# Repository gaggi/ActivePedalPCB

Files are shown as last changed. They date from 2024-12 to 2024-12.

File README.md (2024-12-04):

# Switch-!t ActivePedalPCB
This is a custom PCB designed for the [DIY Force Feedback Pedal](https://github.com/ChrGri/DIY-Sim-Racing-FFB-Pedal). Similar to the V4 PCB from the previously mentioned repository, it is designed to accommodate all the required development and breakout boards. The PCB is built around the Waveshare [ESP32-S3-DEV-Kit-N8R8](https://www.waveshare.com/wiki/ESP32-S3-DEV-KIT-N8R8) and features only five SMD components that need to be soldered by hand.

It is intended to operate via a single USB-B connector for each pedal, powered by a single Meanwell GST360B36-C6P power supply. The power supply can be daisy-chained from one pedal to another. Additionally, the PCB includes space for an optional N7805 step-down converter, enabling all electronics to be powered directly by the power supply. If you choose to solder the N7805, ensure that the 5V connection from the JST-XH header labeled "USB" to the USB-C plug remains unconnected.

# Soldering you PCB
The PCB is designed to allow sub-boards to be attached using female headers or soldered directly to the board. If you opt for direct soldering, follow these steps:
1. Front Side: Start by soldering the SMD components, then solder the pin headers for the ESP32-S3-DEV-KIT-N8R8.
2. Back Side: Solder the ADS1256 module.
3. Front Side: ESP32-S3-DEV-KIT-N8R8: Attach it to the already soldered headers.
   
Once these steps are complete, you can solder all remaining components to the PCB.

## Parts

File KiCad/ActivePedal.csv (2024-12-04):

Reference | Value | Datasheet | Footprint | Qty | DNP | Mouser Part Number | Mouser Price/Stock
J3 | Conn_01x05 | ~ | Connector_JST:JST_XH_B5B-XH-A_1x05_P2.50mm_Vertical | 1
U1 | ESP32-S3-DEV-KIT-N8R8 |  | PCM_Espressif:ESP32-S3-DEV-KIT-N8R8 | 1
U2 | ADS1256_Breakout | http://www.ti.com/lit/ds/symlink/ads1243.pdf | ADS1256_Breakout:ADS1256_Breakout | 1
U3 | ~ |  | Levelshifter_Breakout:Levelshifter_Breakout | 1
J4,J9,J10,J11 | Conn_01x02 | ~ | -- verschiedene Werte -- | 4 |  | 306-B2BXH2TV4LFSN
J1,J5 | Conn_01x04 | ~ | Connector_JST:JST_XH_B4B-XH-A_1x04_P2.50mm_Vertical | 2 |  | 306-B4BXH2TV4LFSN
J2 | Conn_01x03 | ~ | Connector_JST:JST_XH_B3B-XH-A_1x03_P2.50mm_Vertical | 1 |  | 306-BH3BXH2LFSN
J7,J8 | Conn_02x03_Top_Bottom | ~ | Connector_Molex:Molex_Mini-Fit_Jr_5569-06A2_2x03_P4.20mm_Horizontal | 2 |  | 538-26-01-3116
D1 | SS510B | ~ | Diode_SMD:D_SMA-SMB_Universal_Handsoldering | 1 |  | 621-SDT5A50SAF-13
J6 | USB_B | ~ | Connector_USB:USB_B_OST_USB-B1HSxx_Horizontal | 1 |  | 640-USB1030-GF-P-B-B
SW1 | SW_DIP_x02 | ~ | Button_Switch_THT:SW_DIP_SPSTx02_Slide_9.78x7.26mm_W7.62mm_P2.54mm | 1 |  | 655-1825360-1
R1 | 100k | ~ | Resistor_SMD:R_1206_3216Metric_Pad1.30x1.75mm_HandSolder | 1 |  | 708-RNCF1206BTE100K
PS1 | N7805-1PH | https://www.meanwell.com/webapp/product/search.aspx?prod=N78 | N7805-1PH:N78051PH | 1 |  | 709-N7805-1PH | https://www.mouser.co.uk/ProductDetail/MEAN-WELL/N7805-1PH?qs=7D1LtPJG0i2yQtENgJv8Bw%3D%3D
C1 | 10µF | ~ | Capacitor_SMD:CP_Elec_6.3x5.9 | 1 |  | 710-865080743010
C2,C3 | 330µF | ~ | Capacitor_SMD:CP_Elec_10x10 | 2 |  | 710-865230657014

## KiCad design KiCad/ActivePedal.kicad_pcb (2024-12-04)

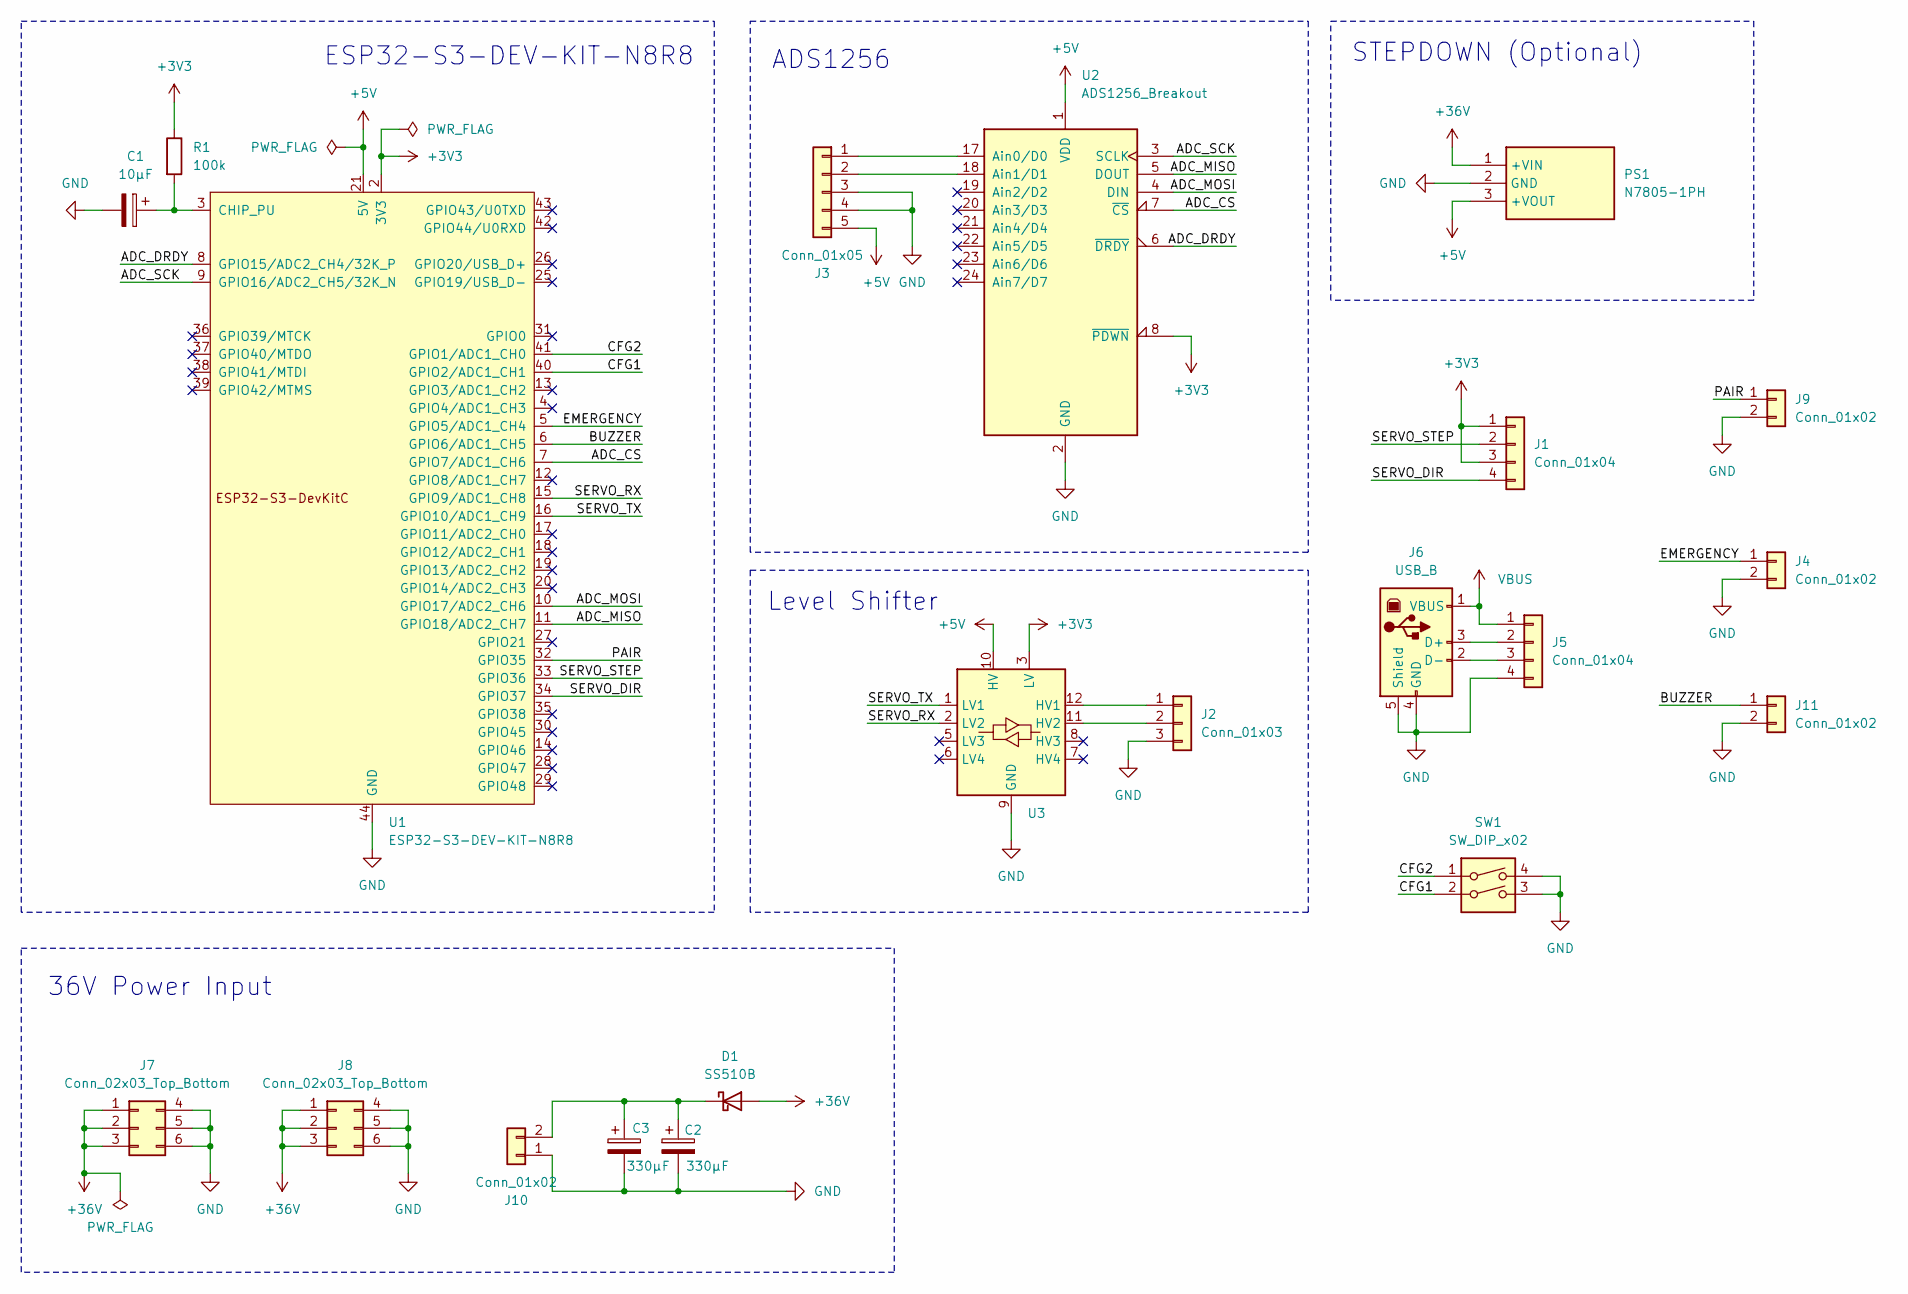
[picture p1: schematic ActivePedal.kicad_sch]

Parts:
C1: 10µF; CP_Elec_6.3x5.9; Mouser Part Number 710-865080743010
C2, C3: 330µF; CP_Elec_10x10; Mouser Part Number 710-865230657014
D1: SS510B; D_SMA-SMB_Universal_Handsoldering; Mouser Part Number 621-SDT5A50SAF-13
J1, J5: Conn_01x04; JST_XH_B4B-XH-A_1x04_P2.50mm_Vertical; Mouser Part Number 306-B4BXH2TV4LFSN
J2: Conn_01x03; JST_XH_B3B-XH-A_1x03_P2.50mm_Vertical; Mouser Part Number 306-BH3BXH2LFSN
J3: Conn_01x05; JST_XH_B5B-XH-A_1x05_P2.50mm_Vertical
J4, J9, J11: Conn_01x02; JST_XH_B2B-XH-A_1x02_P2.50mm_Vertical; Mouser Part Number 306-B2BXH2TV4LFSN
J6: USB_B; USB_B_OST_USB-B1HSxx_Horizontal; Mouser Part Number 640-USB1030-GF-P-B-B
J7, J8: Conn_02x03_Top_Bottom; Molex_Mini-Fit_Jr_5569-06A2_2x03_P4.20mm_Horizontal; Mouser Part Number 538-26-01-3116
J10: Conn_01x02; AMASS_XT30U-F_1x02_P5.0mm_Vertical; Mouser Part Number 306-B2BXH2TV4LFSN
PS1: N7805-1PH; N78051PH; Mouser Part Number 709-N7805-1PH
R1: 100k; R_1206_3216Metric_Pad1.30x1.75mm_HandSolder; Mouser Part Number 708-RNCF1206BTE100K
SW1: SW_DIP_x02; SW_DIP_SPSTx02_Slide_9.78x7.26mm_W7.62mm_P2.54mm; Mouser Part Number 655-1825360-1
U1: ESP32-S3-DEV-KIT-N8R8
U2: ADS1256_Breakout
U3: Levelshifter_Breakout

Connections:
+3V3: J1.1, J1.3, R1.1, U1.1 (3V3), U1.2 (3V3), U2.8 (~PDWN), U3.3 (LV)
+5V: J3.5, PS1.3 (+VOUT), U1.21 (5V), U2.1 (VDD), U3.10 (HV)
+36V: D1.2 (A), J7.1, J7.2, J7.3, J8.1, J8.2, J8.3, PS1.1 (+VIN)
/ADC_CS: U1.7 (GPIO7/ADC1_CH6), U2.7 (~CS)
/ADC_DRDY: U1.8 (GPIO15/ADC2_CH4/32K_P), U2.6 (~DRDY)
/ADC_MISO: U1.11 (GPIO18/ADC2_CH7), U2.5 (DOUT)
/ADC_MOSI: U1.10 (GPIO17/ADC2_CH6), U2.4 (DIN)
/ADC_SCK: U1.9 (GPIO16/ADC2_CH5/32K_N), U2.3 (SCLK)
/BUZZER: J11.1, U1.6 (GPIO6/ADC1_CH5)
/CFG1: SW1.2, U1.40 (GPIO2/ADC1_CH1)
/CFG2: SW1.1, U1.41 (GPIO1/ADC1_CH0)
/EMERGENCY: J4.1, U1.5 (GPIO5/ADC1_CH4)
/PAIR: J9.1, U1.32 (GPIO35)
/SERVO_DIR: J1.4, U1.34 (GPIO37)
/SERVO_RX: U1.15 (GPIO9/ADC1_CH8), U3.2 (LV2)
/SERVO_STEP: J1.2, U1.33 (GPIO36)
/SERVO_TX: U1.16 (GPIO10/ADC1_CH9), U3.1 (LV1)
GND: C1.2, C2.2, C3.2, J2.3, J3.3, J3.4, J4.2, J5.4, J6.4 (GND), J6.5 (Shield), J7.4, J7.5, J7.6, J8.4, J8.5, J8.6, J9.2, J10.1, J11.2, PS1.2 (GND), SW1.3, SW1.4, U1.22 (GND), U1.23 (GND), U1.24 (GND), U1.44 (GND), U2.2 (GND), U2.9 (GND), U2.10 (GND), U2.11 (GND), U2.12 (GND), U2.13 (GND), U2.14 (GND), U2.15 (GND), U2.16 (GND), U3.4 (GND), U3.9 (GND)
unnamed: C2.1, C3.1, D1.1 (K), J10.2
unnamed: J2.1, U3.12 (HV1)
unnamed: J2.2, U3.11 (HV2)
unnamed: J3.1, U2.17 (Ain0/D0)
unnamed: J3.2, U2.18 (Ain1/D1)
unnamed: J5.2, J6.3 (D+)
unnamed: J5.3, J6.2 (D-)
unnamed: C1.1, R1.2, U1.3 (CHIP_PU)
VBUS: J5.1, J6.1 (VBUS)

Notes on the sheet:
ESP32-S3-DEV-KIT-N8R8
ADS1256
36V Power Input
STEPDOWN (Optional)
Level Shifter

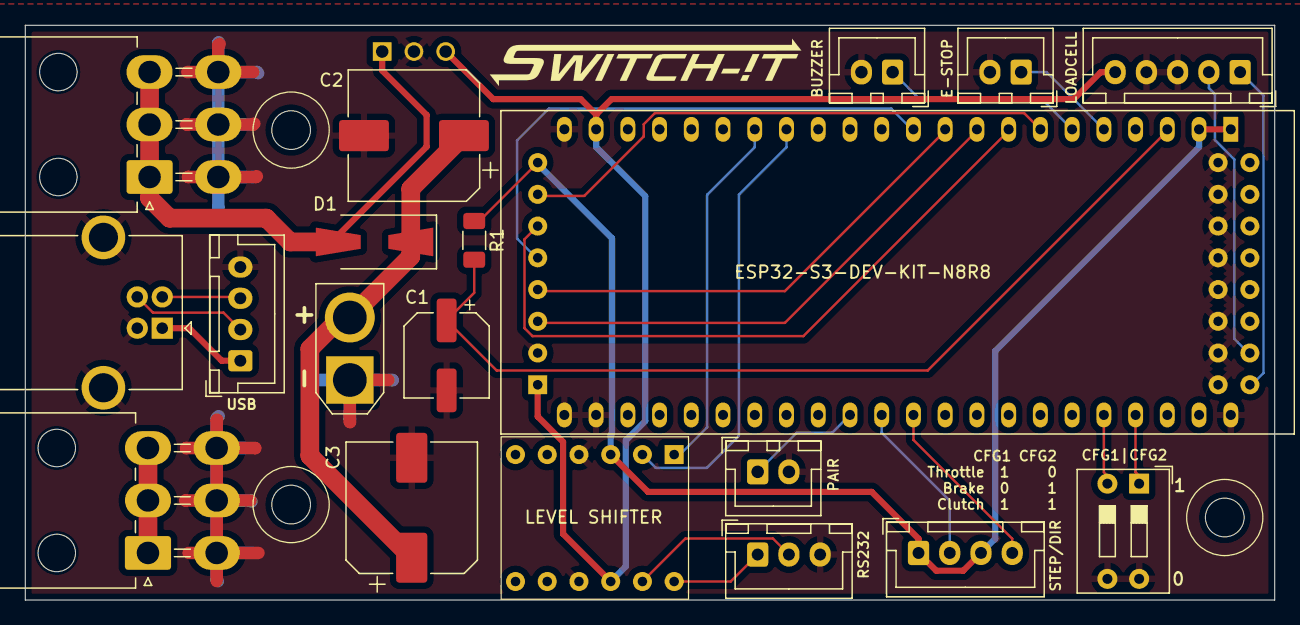
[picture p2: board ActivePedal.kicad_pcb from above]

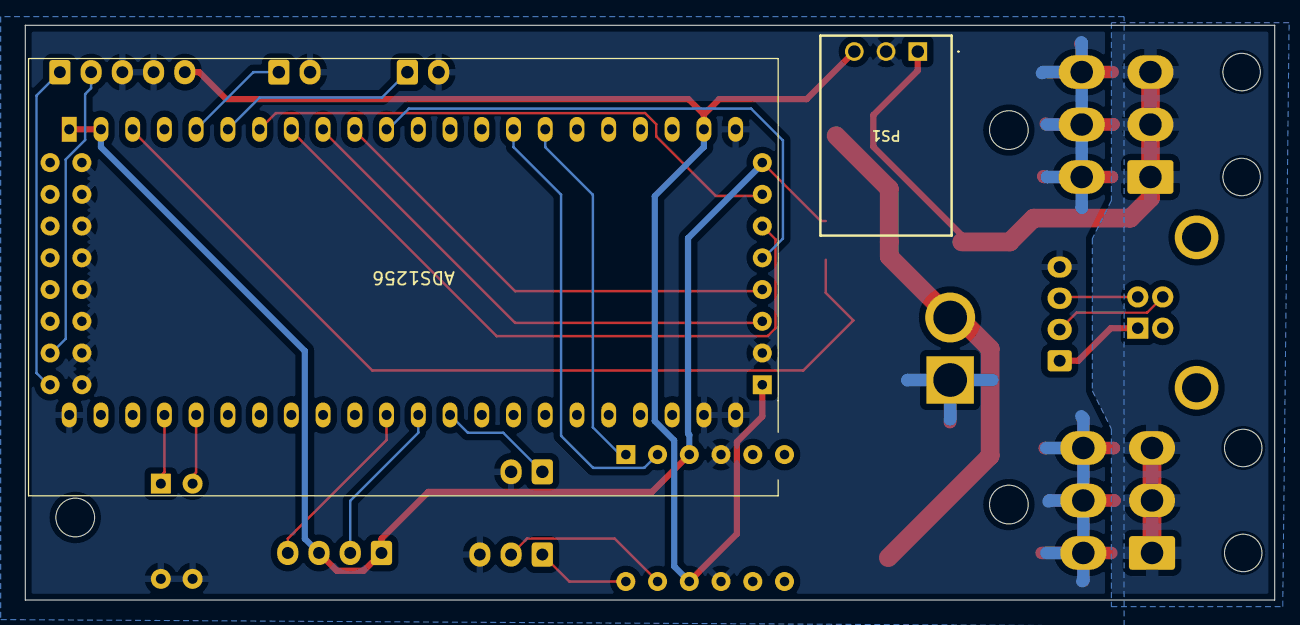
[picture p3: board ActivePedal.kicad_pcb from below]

Board: 2 copper layers, 100.0 x 46.0 mm, 21 parts (2 on the bottom side), 27 nets.
